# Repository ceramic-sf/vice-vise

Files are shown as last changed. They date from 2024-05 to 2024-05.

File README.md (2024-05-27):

# vice-vise
A vise powered by an inverted planetary roller screw

It is a vise and a play thing with a removable mechanism. 3D print it, use it, understand it
and use a roller screw in your next project.

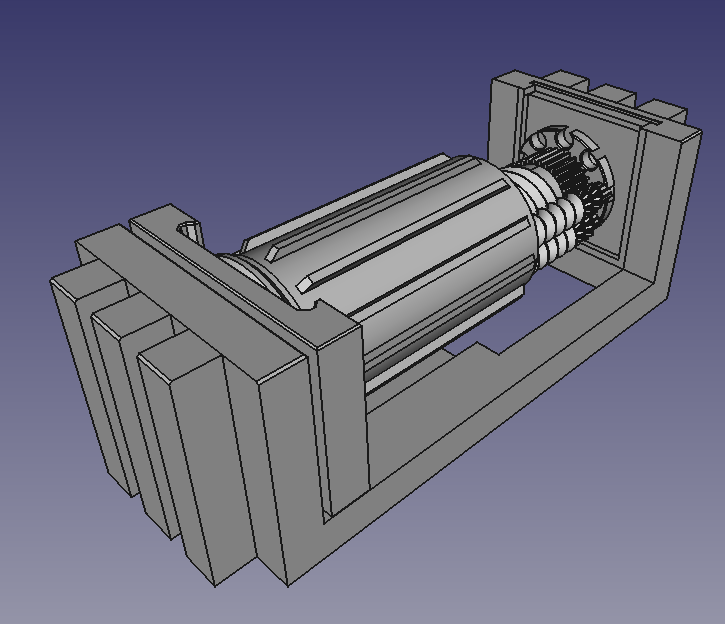
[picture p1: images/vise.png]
vise


### Free

Open free hardware, please use as you see fit.

open_hardware

### Practical

The vise actually works and is quite nice to use. It has the benefit of being easy
to drive without a large handle. Simply roll your palm to spin it open or closed.

### Fun

The roller screw is fun to learn about and very satisfying to play with and inspect.
The internal core of the mechanism often ends up in one's hands when deep in thought. A true vice.

### Tangible

The roller screw mechanism has a few parameters that affect its performance.
Print different variations of the mechanism and swap them out to compare the effect.

Some run faster, some with more force, some feel more robust. Get a tactical
appreciation of the difference.

### Helpful

If you need a mechanism for linear movement, a roller screw may be good for you.

The FreeCAD model provided uses a parametric design, so you can adjust the model to your needs.
Remove the vise parts and add on anything else you like.

If you prefer to start over in a different CAD software, use the [`roller_screw_recipe.md`](roller_screw_recipe.md)
to see what steps to follow when designing an inverted planetary roller screw.

### Science

I discovered the equations for roller screws weren't working, and made up some new ones that you
can use.

The planetary roller screw (PRS) and inverted planetary roller screw (IPRS) have a subtle difference that mean
the dimensions of their components are different.

For a roller screw with a given number of thread starts and nut radius, the screw and roller radii are as follows:

| | PRS | IPRS |
|---|---|---|
| screw  | `nut * (starts - 2 ) / starts` | `nut * starts / (starts + 2)` |
| roller | `nut / starts` | `nut / (starts + 2)`  |

This is of interest for two reasons:
- It is required to design an inverted planetary roller screw.
- It shows that where a planetary roller screw must have >2 starts to have a non-zero screw size.

A inverted roller screw can therefore have 1 or 2 starts, which may be of interest when optimising for high mechanical advantage.

See [https://github.com/ceramic-sf/iprs-geometry](https://github.com/ceramic-sf/iprs-geometry) for a full exploration and derivation.

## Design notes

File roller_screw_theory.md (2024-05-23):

# Inverted Planetary Roller Screw

A low friction mechanism that translates rotation into linear movement with high mechanical advantage

Roller screws are useful if you have a load-bearing linear actuator and want to push the frontier in one of:
- Faster speed
- Larger force
- Lower power

## Contents

  - [Terminology](#terminology)
  - [Name](#name)
  - [Function](#function)
  - [Mechanism tradeoffs](#mechanism-tradeoffs)
  - [Mechanical advantage](#mechanical-advantage)
  - [Function of a regular screw](#function-of-a-regular-screw)
  - [Benefit of an efficient screw (roller screw)](#benefit-of-an-efficient-screw-roller-screw)
  - [Roller screw parameters](#roller-screw-parameters)
  - [How parts rotate](#how-parts-rotate)
  - [Intuition for main action](#intuition-for-main-action)
  - [Threads](#threads)
  - [Planetary roller screw vs inverted planetary roller screw](#planetary-roller-screw-vs-inverted-planetary-roller-screw)
  - [Output force calculation](#output-force-calculation)
  - [Spur gear](#spur-gear)

## Terminology

- Thread start
    - A tooth that spirals around to form a thread. Two starts means
    that at the base there are two teeth that exist. The ridges on the
    thread will alternate, one from each tooth.
- Screw ("Sun")
    - The central core of the mechanism with a thread
- Rollers ("Planets")
    - Smaller cylinders that spin and revolve around the core
    - Have a thread with one start
- Nut ("Ring")
    - Outer cylinder with an internal thread
- Carrier
    - A disk that holds the planets in alignment
- Spur gear (cut on the rollers)
    - Ensures the rollers turn at the right rate
    - The spur gear is cut onto the roller thread so that the spur gear
    does not get in the way of the roller thread meshing with the nut thread.
- Spur gear (either on the screw or the nut)
    - Ensures that the rollers turn at the right rate

## Name

Inverted Planetary Roller Screw

- Inverted: The spur gear is not on the nut. It is on the inner screw.
- Planetary: The rollers orbit the central screw.
- Roller: The planets are elongated compared with a regular planetary gear.
- Screw: The main function of the device is to spiral forward, like a screw.

## Function

The assembled components all fit inside the nut. The assembly drives in and out
of the nut as some part is rotated. The rotated part is either the nut or the screw.

This effectively gives different modes of operation.
    - Turn the screw, hold the nut
        - A motor can drive the screw to convert rotation to linear actuation.
    - Turn the nut, hold the screw
        - The nut can be powered by elecromagnetism to form a compact linear actuator.

The main reason to use the roller screw is that it can turn even when under large loads.

## Mechanism tradeoffs

We trade off complexity to get an efficient mechanism that works under loads.

| Mechanism | Complexity | Friction Kind | Tolerance to load |
|---|---|---|---|
| A rack and pinion | Good. The pinion spins and the rack moves in a line. | Good (rolling) | Bad. If one pushes on the pinion, the force is transmitted to oppose the rotation of the motor. |
| A rack and worm gear | Good. The worm gear is rotated and spins against a rack. The rack moves in a line. | Bad (sliding) | Good. If one pushes on the rack, the teeth on the gear transmits the force along the gear axis, rather than opposing rotation. |
| A screw jack or vise | Good. A screw turns within a nut, which advances the screw. | Bad (sliding). Approximately 20% efficiency. The friction is sliding friction along the contact of the thread. | Good. If one pushes on the nut, the force is transmitted to the screw teeth, which does not oppose the motion. |
| Inverted planetary roller screw | Bad. A screw turns and rotates threaded rollers inside a larger nut. The rollers together act as virtual screw within the nut which moves the screw into the nut. | Good (rolling). Approximately 80% efficiency. The screw rolls on the rollers and the rollers roll on the nut. It is technically sliding friction at each contact point of the rollers. Overall, the action is low friction rolling kind. | Good. If one pushes on the nut, the force is transmitted to the roller teeth then to the screw teeth, then to the axis of the motor, rather than opposing the rotation of the motor. |

## Mechanical advantage

When the screw is driven by an input torque, the output force is subject
to a multiplier as follows:
```
force_out = torque_in * 2 * pi / (num_starts * thread_pitch_meters)
```
The derivation of the equation is covered in a later section.

For example a thread with one start and a 6mm (0.006m) pitch would result in
a mechanical advantage of 1000x. A 10NM input torque could generate 10kN of force
in a frictionless environment.

## Function of a regular screw

Screws have tremendous ability to turn an input torque into a large force.
Consider a vise, which uses the lead screw to apply a large force.

To understand this, consider a perfectly efficient vise with a very long lead screw. With a lead of 6.3m (2 * pi), the screw has no mechanical advantage. An input of 10Nm torque would translate to an output force of 10N.

Yet, normal leads are about 1000 times shorter (6mm vs 6m) and the gain is therefore 1000x. So
10Nm input torque creates about 10KN output force. If a screw has terrible efficiency (10%), it can still create 1kN output force.

So, because the neutral lead (6.3m) is so large compared with leads practically used, it does not matter how inefficient a screw is normally. The result is usually "good enough".

## Benefit of an efficient screw (roller screw)

What if screws were 10x more efficient? That is the niche that roller screws fill. Practically, we are talking about clamping a piece of wood with a bench vise with a handle 10x shorter. What are areas where this is actually beneficial?

- Huge forces that stress mechanical parts, like in large industrical presses. A vise can only be used up to the point where the handle starts to bend. A low efficiency means that the handle will bend before higher forces can be delivered.
- Systems sensitive to total energy use. A low efficiency means that a low percentage of energy is being used for the task. So battery based systems (robotics, space industries).
- Systems designed for speed. A low efficiency means that the force being delivered has to be over a short distance (a small lead). An increase in efficiency means the lead can be longer. This means the output force can be delivered over longer distances. This is equivalent to having a vise move faster without sacrificing strength.

A roller screw is an efficient screw, roughly 80-90% vs 10-20% as seen in other
screw based devices (screw jack, vise). This makes them good for heavy industrial processes, robotics, aerospace and performance.

In summary, a the efficiency of a roller screw can be used to get one of:
- Larger output force
- Faster output speed
- Longer output duration

If an application is not already pushing the limits of a particular variable above, then a roller screw adds complexity without a material gain.

## Roller screw parameters

As a screw, the main parameter to control is the lead. For every turn of
the screw, how much does the assembly advance in the nut? A higher lead
gives faster speed but less strength.

The parameter selection is best done as follows:
- Choose the diameter of the nut based on how small the mechanism needs to be
- Choose the thread pitch based on how fine you can manufacture one
- Choose the number of thread starts based on how much gearing you need
- Choose if the device is a precise and low energy application or chunky and high energy (gear modulus)

All remaining parameters basically are derived from the above.

For example. Knowing the thread starts gives you the diameter of the rollers and screw.
That allows the spur gear diameters to be known. Given the approximate modulus,
this allows the spur gear teeth counts and profiles to be derived.

See the recipe page for a more thorough explanation.

## How parts rotate

In a regular planetary gearset, the carrier rotates according to the number
of teeth on the sun and ring gears. That is not the case for the roller screw.

The rollers instead move by rules more akin to how parts of a spirograph move.
The movement of the carrier is determined by the size of the rollers relative to
the screw. This has to do with the least common multiple of these numbers.

This is more academic (or for making perfect animations). Roller screws work by
advancing the assembly in the nut. The number of rotations of the carrier is not
required for gear calculations. In contrast, these numbers are important for regular planetary gearsets where the carrier may be the direct output.

There are two parts to how the assembly advances. Together the result is
the assemble advances one lead length (pitch * starts) per screw rotation.
- Carrier rotation
    - The rollers physically move
    - Related to the sizes of the spur gears (the radius of the screw/rollers)
- Roller rotation
    - The rollers turn
    - Related to the thread starts on the screw. With more starts the rollers turn more because they only have one thread start.

## Intuition for main action

To understand what happens in the roller screw, imagine the set of rollers as a single virtual screw
with the rollers fixed in place. Around the whole set, one can draw a virtual thread that wraps around
all the rollers. With this large virtual screw, one can imagine screwing it into the large nut housing. The rollers simply replicate the thread on the inner screw, but at a larger diameter and in a way that has better friction properties.
If the inner thread has multiple starts, so does the virtual thread.

One can indeed do this with the roller screw setup if is sloppy enough. The rollers can be held
to prevent them rolling and the whole set can be rotated to insert into the nut. However this is
bad because as they move in, the primary interaction is sliding friction. Sliding friction
requires a lot of force and has high energy loss to heat.

Instead, the rollers rotate and orbit around the screw. As each roller turns, its thread turns
and the outermost contact points on the roller shift. Together, the rollers orbit around the screw.
The effect of these two things combined is that a virtual screw is rotating. Imagine a screw whose
contact points keep being replaced by miniature rotation systems. Each roller is one such rotation
system.

In summary, a roller screw is a screw whose surface is a slippery and changing thing. That
is what makes it low friction.

## Threads

Two threaded rods can rotate against each other as helical gears. A thread may have a number of
starts. One start being a single tooth that winds all the way along. Two starts meaning that
every second ridge along the screw is the same tooth.

As the two threaded rods rotate against each other, the thread starts at the end of the rod must line
up to mesh. In this way, they are functionally equivalent to teeth. A rod with 4 starts that rotates
against a rod with 1 start is like a gear ratio of 4 to 1. For every rotation of the first rod, the
second rod rotates 4 times.

## Planetary roller screw vs inverted planetary roller screw

The inverted planetary roller screw (IPRS) has some differences to the regular planetary roller screw (PRS).

The central rod in an IPRS is only threaded for a short distance. This allows an extension rod to be used and for the nut to be sealed and lubricated. A PRS has a screw the entire length of the rod, and cannot be sealed as compactly.

In contrast, a PRS allows the nut to be a short length, rather than having it span the length of the linear travel of the mechanism.

## Output force calculation

For every rotation of the screw, it advances exactly one lead.

Hence for all IPRS driven like this, one rotation will cause linear movement of half the lead
```
linear = lead
```

Consider a rack and pinion. The stepper motor can be imagined as driving the pinion.
For one rotation the rack advances `linear` amount, which is equal to the circumference of the
pinion. The radius of the pinion is therefore:

```
cicumference_pinion = 2 * pi * r_pinion
r_pinion = cicumference_pinion / (2 * pi)
r_pinion = lead / (2 * pi)
```
The stepper is generating torque at that pinion radius. This causes the rack to advance with
a force:
```
torque_stepper = force_rack * radius_pinion
torque_stepper = force_rack * lead / (2 * pi)
force_rack = torque_stepper * 2 * pi / lead
```

If the output rack force is applied at 1m, that will be the output torque in Nm.

The gain calculated as:
```
gain = output / input
gain = force_rack / torque_stepper
gain = (torque_stepper * 2 * pi / lead) / torque_stepper
gain = 2 * pi / lead
```

Hence as the lead increases the torque gain decreases.

If the lead is 16mm, the gain is:
```
gain = 2 * pi / 0.016
gain = 392
```

So the only way to increase the gain is to reduce the lead, which can be achieved either
by reducing the starts and the pitch.
```
lead = num_starts * pitch
```

This demonstrates the fundemental tradeoff: spin the motor more revolutions for a given linear
travel to gain force.

So in the context of the roller screw, this would be:
```
force_out = torque_in * 2 * pi / lead
```
A cheap 0.3Nm stepper motor driving an inverted planetary roller screw with a 10mm (0.01) lead would produce a force of 188N, enough to drive a ~15kg platform updward.

## Spur gear

Roller screws have a spur gear cut into the thread of the rollers. This gives a mechanism to
ensure the rollers are synced with the screw, which prevents them migrating along their axes.
The gear is not a high energy gear, it is only used for timing.

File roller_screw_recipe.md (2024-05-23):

## Recipe

Steps to follow to make an inverted planetary roller screw (IPRS).

For a working CAD model that uses this recipe, see the `model` directory.

  - [Recipe](#recipe)
    - [Main performance parameters](#main-performance-parameters)
    - [Thread tooth](#thread-tooth)
    - [Pitch](#pitch)
    - [Starts](#starts)
    - [Linear speed](#linear-speed)
    - [Mechanical advantage](#mechanical-advantage)
    - [Nut radius](#nut-radius)
    - [Roller diameter](#roller-diameter)
    - [Screw diameter](#screw-diameter)
    - [Screw thread length](#screw-thread-length)
    - [Spur gear length](#spur-gear-length)
    - [Roller length](#roller-length)
    - [Nut length](#nut-length)
    - [Screw surface radius](#screw-surface-radius)
    - [Roller surface radius](#roller-surface-radius)
    - [Nut inner surface radius](#nut-inner-surface-radius)
    - [Spur gear diameters](#spur-gear-diameters)
    - [Spur gear CAD](#spur-gear-cad)
    - [Spur gear teeth](#spur-gear-teeth)
    - [Roller thread](#roller-thread)
    - [Roller count](#roller-count)
    - [Carrier](#carrier)
    - [Circlip](#circlip)
    - [3D printing tips](#3d-printing-tips)
    - [Assembly tips](#assembly-tips)

### Main performance parameters

The screw may have a slow and strong thread, or a fast and weak thread. This
is controlled by two factors, the thread pitch and the thread starts.

| | One Start | Few Starts | Many Starts | Comment |
|---|---|---|---|---|
| Small Pitch | Too slow | Great torque & precision  | Too sensitive to tolerances | Strong & slow, delicate thread |
| Medium Pitch | Great torque & robust | **Choose this one** | Great speed & precision | |
| Large Pitch | Too weak central screw | Great speed & robust | Too senstive to loads | Weak & fast, delicate roller carrier |
| Comment | Slow & strong, big rollers | | Fast & weak, small rollers | |

Select an all rounder by default, something that you can make easily and use reliably and practically.

Screws work by dividng work done over a large distance. The lead of the screw (linear travel per rotation) determines exactly how much torque/precision/speed/robustness. Roller screws do the same but with low friction.

The roller screw gains the benefit of low friction by increased complexity compared to a regular screw. Attempts to optimise too hard (tiny lead, huge lead) can significantly impair an otherwise complex mechanism.

Screws already have a huge mechanical advantage. A frictionless screw that has a lead of 2 * pi (~6 meters) has no mechanical advantage. A 3 meter lead has 2x advantage, and a lead of 6 millimeters has 1000x advantage. Hence, it is the main
priority to get the mechanism produced and reliably operating rather than tweaking the lead to get slightly better mechanical advantage.

### Thread tooth

The teeth on all the threads (rollers, screw, nut) are the same.

The tooth is wrapped around a cylinder to make the thread. The base of the tooth is equal to the thread pitch. The height of the tooth depends angle in the apex of the tooth.

A triangle with 90 degrees at the apex is standard, but other profiles (60 degrees) may work.

Some sources recommend optimising the teeth of the roller thread by making them slightly convex to reduce friction. For a basic construction a simple straight edge may be used, which allows reuse of the tooth profile for the screw, roller and nut.

### Pitch

The distance between adjacent ridges of the thread. This will be the base of the tooth triangle.
As such, this also controls how tall the tooth is.

As pitch increases, the torque drops and speed increases.

A small pitch may be hard to manufacture. A large pitch may make the teeth too big to fit
in the roller screw.

### Starts

With the pitch selected the actual lead of the screw can now be decided. This is how much linear distance will be traveled per full rotation of the mechanism (either the nut or the screw).
```
lead = pitch * thread_starts
```

| Lead | 1 Start | 2 Starts | 3 Starts | 4 Starts |
|---|---|---|---|---|
| 4mm Pitch | 4mm | 8mm | 12mm | 16mm |
| 8mm Pitch | 8mm | 16mm | 24mm | 32mm |
| 12mm Pitch | 12mm | 24mm | 36mm | 48mm |

### Linear speed

If the roller screw is being driven by a motor, then the maximum rotation of the motor will determine the maximum linear speed of the final mechanism.
For a motor with a certain rotations per minute (RPM):

```
linear_speed_per_second = motor_rpm * lead / 60
```
This may help inform the selection of the pitch and thread starts.
However, speed is inversely related to mechanical advantage.

### Mechanical advantage

Now that the lead is known, the mechanical advantage can be calculated.

Consider a screw driven by 1 Nm of torque for a full rotation. The screw will
extert a constant linear force.
```
force_out = torque_in * 2 * pi / lead_meters
```

|Force out from 1 Nm input| 1 Start | 2 Starts | 3 Starts | 4 Starts |
|---|---|---|---|---|
| 4mm Pitch | 1570 N | 785 N | 523 N | 392 N |
| 8mm Pitch | 785 N | 392 N | 261 N | 196 N |
| 12mm Pitch | 523 N | 261 N | 174 N | 130 N |

So the bottom right configuration may have 12x faster linear travel, but 12x less force during that distance.

As an example, a cheap NEMA17 stepper motor such as those found on basic 3D printers may have 0.3Nm of torque. That motor could power the roller screw to lift a platform upward. The maximum amount of weight it could lift would be as follows. Note that twice the lift means half the speed.

| Lifting capacity of 0.3 Nm motor | 1 Start | 2 Starts | 3 Starts | 4 Starts |
|---|---|---|---|---|
| 4mm Pitch | 47 kg | 24 kg | 16 kg | 12 kg |
| 8mm Pitch | 24 kg | 12 kg | 7.8 kg | 5.9 kg |
| 12mm Pitch | 16 kg | 7.8 kg | 5.2 kg | 3.9 kg |

This ignores friction, which for roller screws would result in ~10-20% loss.

### Nut radius

How wide can you make the cylinder of the roller screw? Where will it be used? Pick the largest you can tolerate,
as this gives the most choice in performance for other parameters.
If the nut is very large, rollers that are a small fraction of the nut size may be easier to manufacture.
```
radius_nut
```

### Roller diameter

Now that starts are known the roller size can be calculated as follows:
```
radius_roller = radius_nut / (num_starts + 2)
```

As the nut contains the screw and the rollers, their radii follow (nut must fit 2 rollers and one screw across the diameter).

The rollers always have one thread start. As the number of thread starts increases, the rollers complete more turns per revolution of the nut or screw.
As they rotate faster, they must be smaller in order to complete full turns.

|| 1 Start | 2 Starts | 3 Starts | 4 Starts | 5 Starts |
|---|---|---|---|---|---|
|  `radius_roller`  | `r_nut / 3` | `r_nut / 4`  | `r_nut / 5`| `r_nut / 6` |`r_nut / 7`|

### Screw diameter

```
radius_screw = radius_nut * (num_starts / (num_starts + 2))
```

|| 1 Start | 2 Starts | 3 Starts | 4 Starts | 5 Starts |
|---|---|---|---|---|---|
|  radius_screw  | `r_nut / 3`| `r_nut / 2`| `r_nut * 3 / 5`| `r_nut * 2 / 3`|`nut * 5 / 7`|

### Screw thread length

Teeth on the rollers engage in the screw and nut and distribute load. The
longer the screw, the less load on each tooth.

A longer screw also increases the stability of the mechanism. Too long, and it will take up linear space and lose some efficiency.

### Spur gear length

Before and after the screw thread, there is a spur gear on the screw. This engages
with the roller and ensures they move correctly.

The spur gear on the planets is cut axially onto the ends of each roller. The
axial length of the spur gear should be at least a few multiples of the pitch, so that the spur gear teeth are always engaged with the planet teeth.
```
spur_gear_length >= 3 * pitch
```

### Roller length

The rollers must be long enough to engage with the screw thread and the two screw spur gears.
```
roller_length = screw_thread_length + 2 * spur_gear_length
```
### Nut length

Determines how far the mechanism can travel. Flexible, but at least as long as the planets. When the same length, the roller screw leaves the nut, which means fewer teeth engaged for strength and stability.

```
nut_length >= roller_length
```

Optimally, screw is extended by a rod so that the mechanism is always inside the nut. This would also enable the mechanism to be sealed and lubricated. If the rod was equal to the roller lenght, and the nut twice the roller length, then the mechanism could safely travel linearly a distance equal to the roller length.

### Screw surface radius

The calculations of the perfect radii of the nut, screw and rollers above is
for the pitch line. This is the line where two cylinders meet perfectly and
have identical surface velocities at this point.

In reality the the surfaces have teeth, which are sometimes above and sometimes below this line. There will be some minor friction as the teeth mesh imperfectly. The tooth should be half above and half below this line.

To create the thread, create a cylinder, place the tooth and do a helical pad.
The helix should travel one lead per revolution. Use a polar pattern for the number of thread starts.

The radius of the screw and roller cylinders will be their pitch radius minus half the tooth height. For the nut, the pitch radius plus half the tooth height.
For a 45 degree tooth this will be `(pitch / 2) / 2`.

```
screw_body_radius = screw_ideal_radius - thread_pitch / 4
```
### Roller surface radius

Similar to the screw, the roller surface on which the thread is added is:

```
roller_body_radius = roller_ideal_radius - thread_pitch / 4
```

The roller body radius is important because this engages with the carrier, and will be weak if too small. One can see that if the thread pitch cannot be larger than `4 * roller_ideal_radius`.

### Nut inner surface radius

As a cylinder, the thread is applied to the inner surface of the nut, and so the
radius will be larger than the pitch line.

```
nut_body_radius = nut_ideal_radius + thread_pitch / 4
```

One can see that once the structural component of the nut is added, the widest point of the roller screw assembly will be `nut_body_radius + nut_wall_thickness`

### Spur gear diameters

The spur gear will have the same pitch line as the main screw pitch line.
Its purpose is to make sure each roller does not over or under rotate, which would cause axial migration.

```
screw_spur_pitch_radius = screw_ideal_radius
```
The screw spur gear will mesh with a spur gear that is cut onto the end of the roller (like a cookie cutter pushed onto the end).
```
roller_spur_pitch_radius = roller_ideal_radius
```

### Spur gear CAD

To create the gear in CAD, use a involute gear design with the module and tooth count. For the screw, pad the
gear shape. For the roller, pad the gear, then create a cylinder and then XOR to create a
cookie-cutter with a spur gear shaped hole. Place one on each end of the roller and use the cut tool
to cut the thread.

### Spur gear teeth

Two spur gears will mesh if they have the same module.
```
module = pitch_diameter / tooth_count
```

One way to think of the module is as a proxy for the energy involved.

| **Module (mm)** | **Purpose** |
|---|---|
| 0.1 - 0.5 | Ultra-fine precision |
| 0.5 - 1.0 | Compact, precise mechanisms |
| 1.0 - 2.0 | General purpose precision |
| 2.0 - 4.0 | Moderate load systems |
| 4.0 - 6.0 | Higher load-bearing machinery |
| 6.0 - 10.0 | Large-scale, high-load systems |
| 10.0+ | Very large |

Experimentally, a module of about 1.25 works well.

First work out exactly what module will give a whole number of teeth:

```
tooth_count ~= pitch_diameter / approx_module
```
Using a floor calculation allows this to be automated.
```
screw_spur_tooth_count = floor(screw_pitch_diameter / 1.25)
```

Actual module:
```
actual_module = screw_pitch_diameter / screw_spur_tooth_count
```
Then find the roller tooth count
```
roller_spur_tooth_count = roller_pitch_diameter / actual_module
```

### Roller thread

The rollers only one thread start, even when the screw and nut have more.
This means that the lead of a roller itself will be the same as the pitch.

Additionally, the roller thread is the opposite direction of the screw and nut threads. That is, a roller screw with a right hand thread will have right hand nut and screw, but left hand rollers. Turning such a screw in a clockwise direction would advance the screw and roller assembly forward into the nut.

### Roller count

The number of rolllers is flexible and one gains strength and stability
by adding more. More rollers can fit with more screw thread starts a smaller
pitch.

### Carrier

The ends of the rollers must have a portion without a thread. These fit into
a carrier, whose role is make it easy to align the rollers during assembly
and to prevent misalignment during operation.

The carrier need only be thick enough to be robust. It spins passively and
does not transmit load like in traditional planetary gearsets.

### Circlip

A clip placed on the screw to keep the carrier in place. A groove is placed on the screw to keep the circlip from moving axially.

### 3D printing tips

Some tips:
- Print rollers separately and with a raft as they may fall over during printing
- Print all threads vertically (standing up) so their surfaces are smooth when rotating

### Assembly tips

- Place rollers in hand, then the screw on top, then wrap two rubber bands around to keep them
all together.
- Move the rollers around under the rubber bands until they are evenly spaced.
- For each roller rotate in place until it is symmetrical relative to the spur gears. Rotation
to the next spur gear tooth will cause the roller to migrate along its axis.
- Add both carriers and circlips, hold the planets and turn the screw.
If there is clicking, find which roller is
responsible and whether it is a print artefact or alignment problem. If needed,
remove one carrier and rotate the rod one spur tooth and try again.

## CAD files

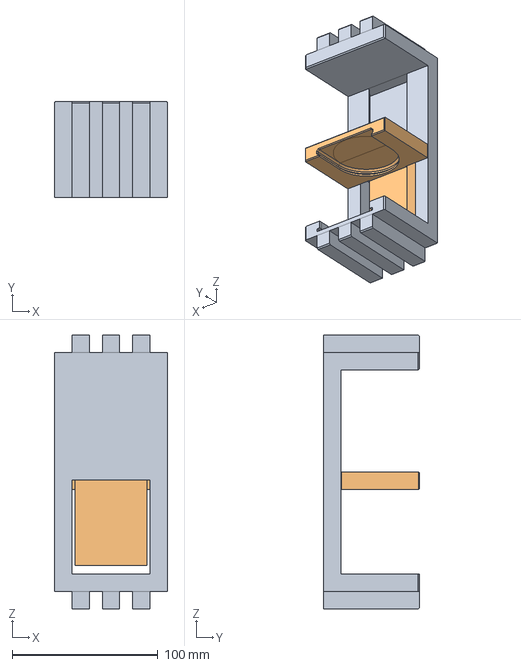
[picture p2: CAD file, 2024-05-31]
models/base.FCStd
77.7 x 66.1 x 188.0 mm
base_body
jaw_body

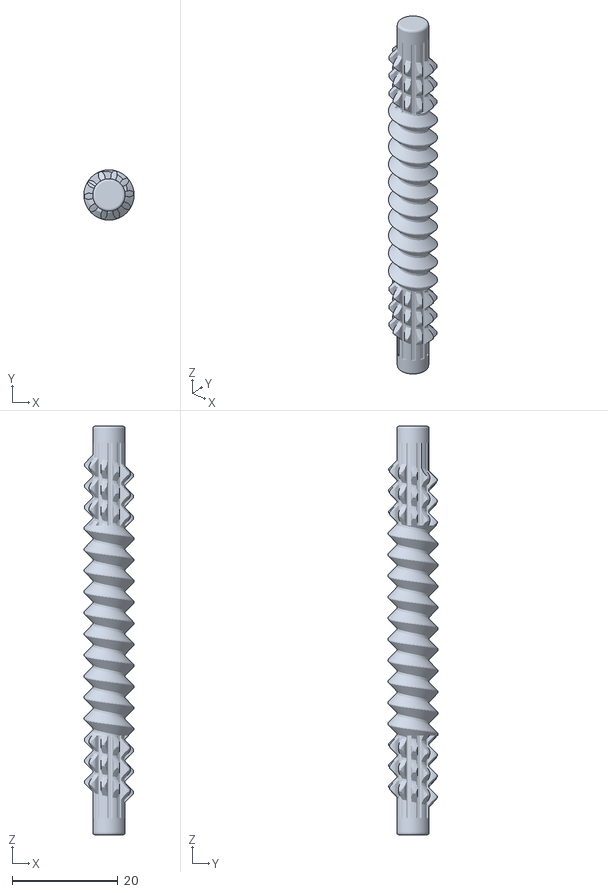
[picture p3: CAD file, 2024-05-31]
models/stl/roller.stl
9.51 x 9.51 x 77.4

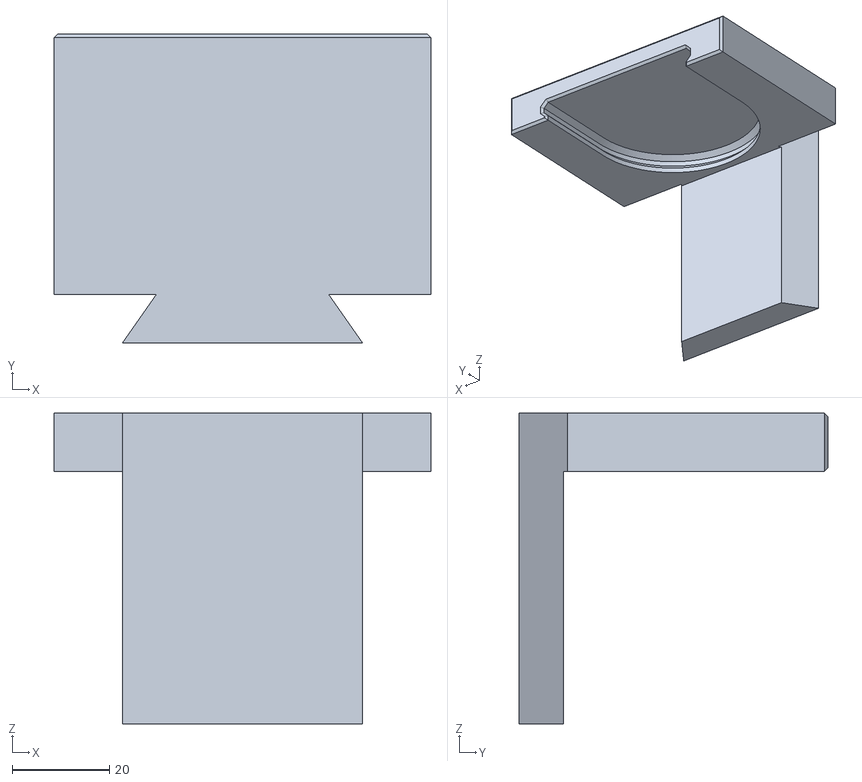
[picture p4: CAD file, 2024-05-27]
models/stl/jaw.stl
77.7 x 63.7 x 64.0

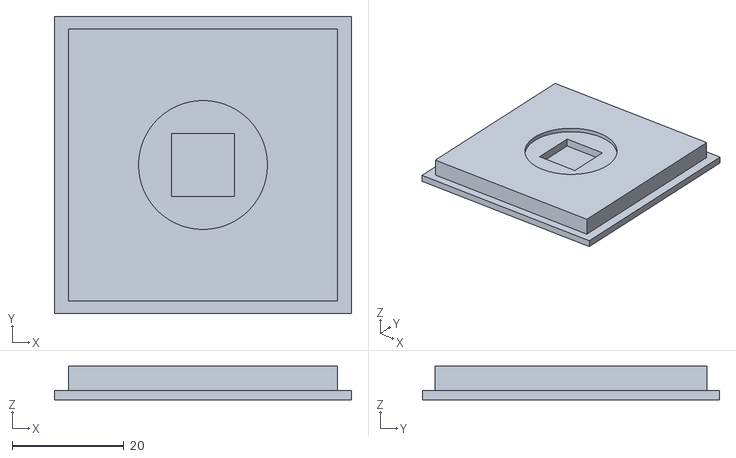
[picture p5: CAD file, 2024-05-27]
models/stl/connector.stl
53.1 x 53.1 x 6.00

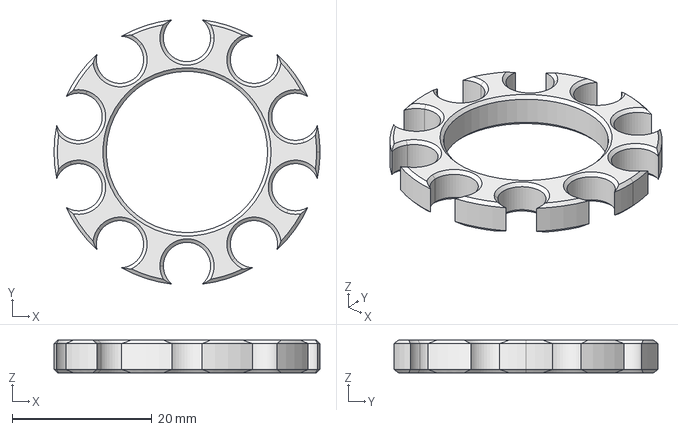
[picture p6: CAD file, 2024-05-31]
models/carrier.FCStd
38.0 x 37.8 x 4.70 mm

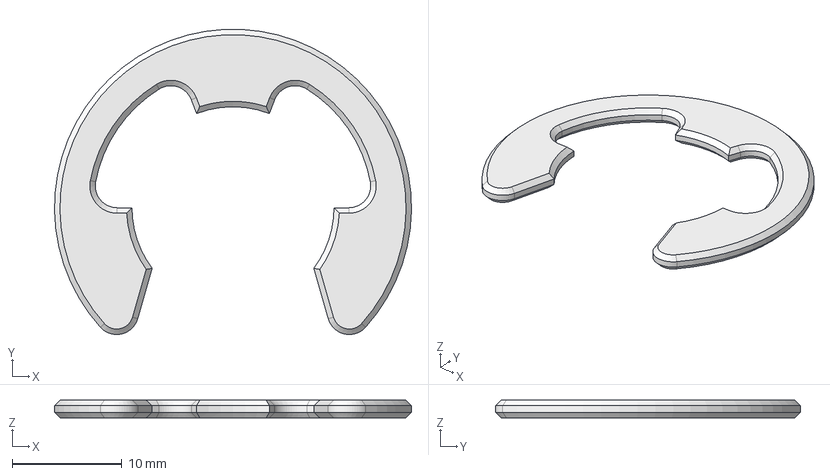
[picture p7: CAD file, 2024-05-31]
models/circlip.FCStd
32.6 x 27.8 x 1.60 mm

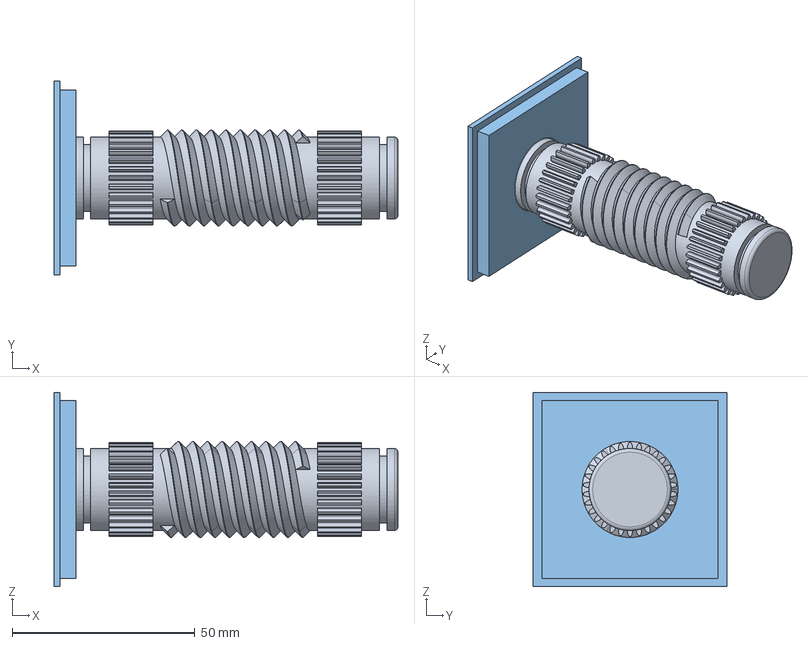
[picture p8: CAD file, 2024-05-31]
models/rod.FCStd
94.0 x 53.1 x 53.1 mm
rod_body
rod_connector_body
rod_cube_body

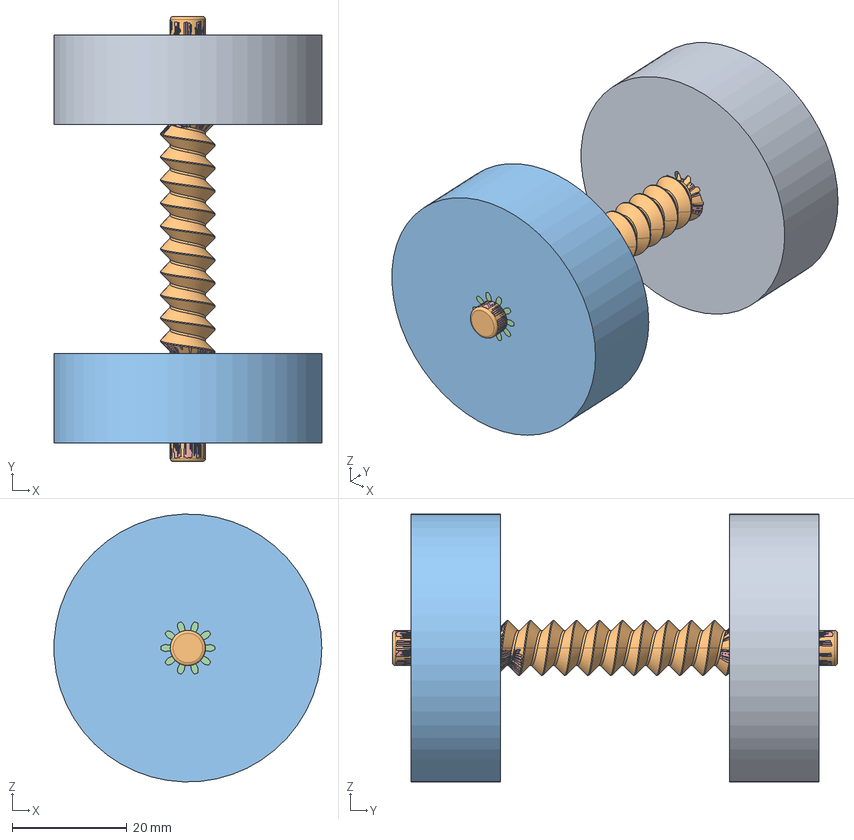
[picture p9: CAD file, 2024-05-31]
models/planetary.FCStd
46.6 x 77.4 x 46.6 mm
gear_cutter_2
planetary_body
gear_negative
planet_spur_gear_body

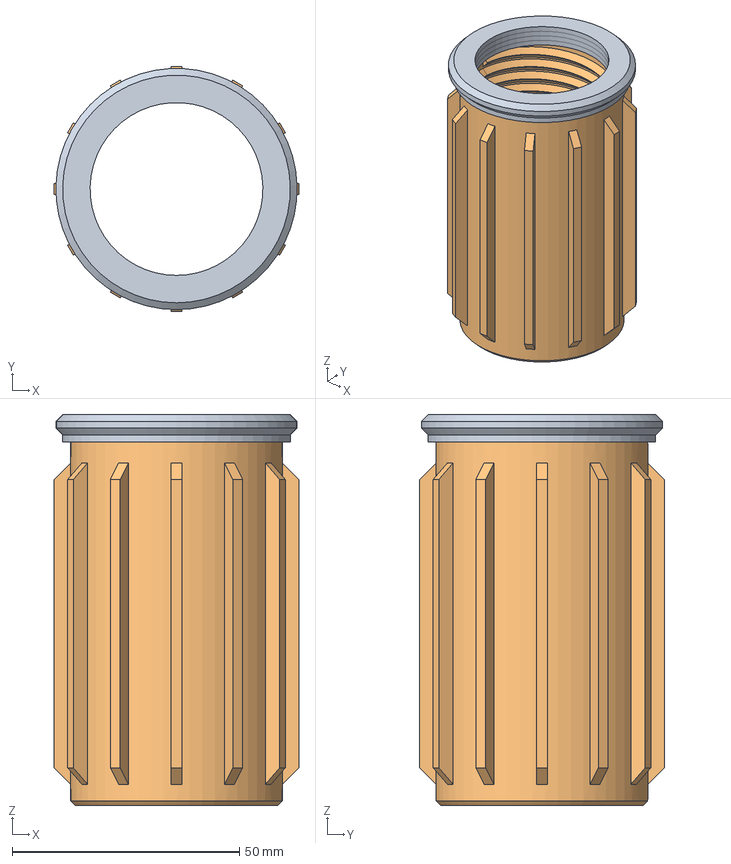
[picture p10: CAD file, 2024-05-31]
models/nut.FCStd
53.9 x 53.9 x 86.0 mm
joining_plate_body
nut_body

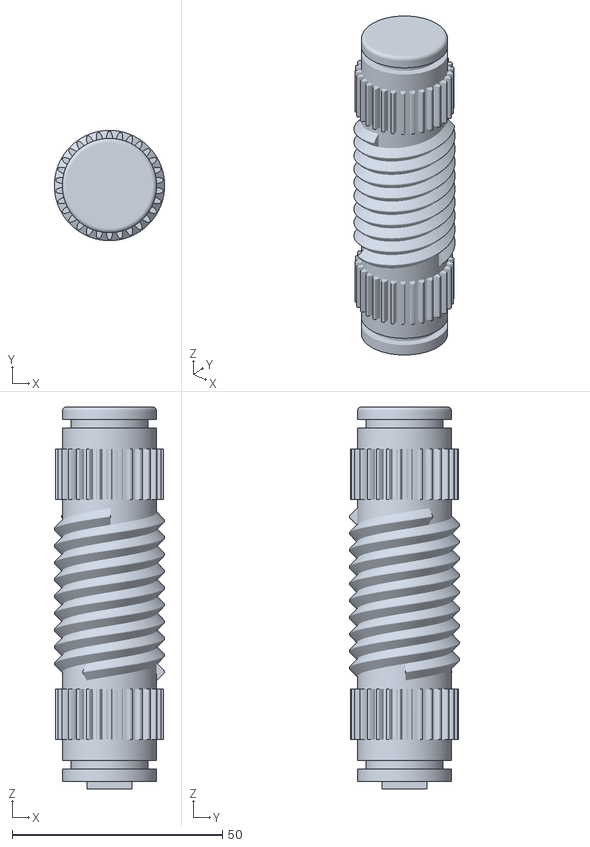
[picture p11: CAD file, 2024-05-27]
models/stl/screw.stl
26.2 x 26.2 x 90.8

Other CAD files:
models/vice_vise.FCStd
models/thread.FCStd
models/params.FCStd
models/stl/base.stl
models/stl/carrier.stl
models/stl/circlip.stl
models/stl/nut.stl

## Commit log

2024-05-23 add models
    [base.FCStd, carrier.FCStd, circlip.FCStd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]
2024-05-27 reduce model default size by 60 percent
    [base.FCStd, carrier.FCStd, circlip.FCStd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]
2024-05-27 add stl files
    [base.stl, carrier.stl, circlip.stl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]
2024-05-31 reduce model scale by 60 percent
    [base.FCStd, carrier.FCStd, carrier.stl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]
